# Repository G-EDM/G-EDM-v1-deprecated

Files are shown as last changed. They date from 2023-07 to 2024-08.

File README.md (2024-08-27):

Deprecated! Check the other repos for the new G-EDM EVOII stuff.

Check out the new Gantry router: https://github.com/G-EDM/GEDM-EVO2-CNC

# New design, new code, new sensing... Coming soon. 

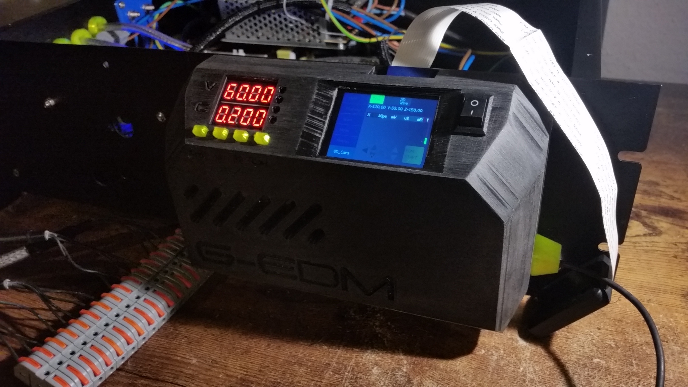
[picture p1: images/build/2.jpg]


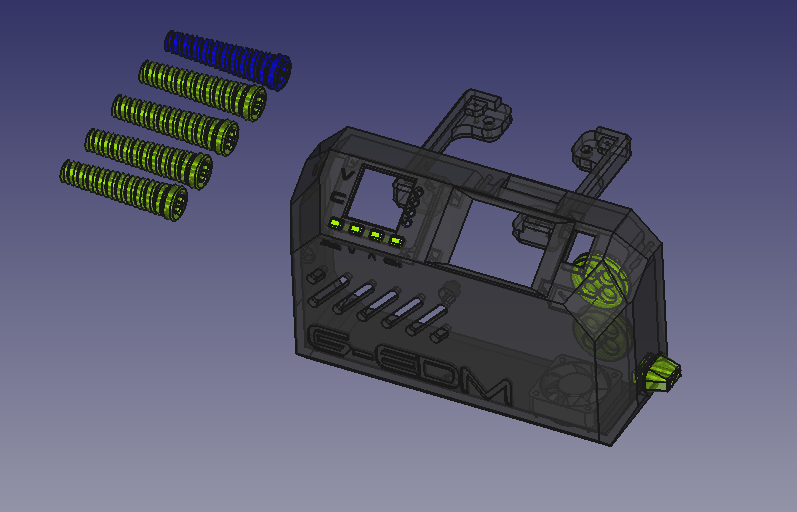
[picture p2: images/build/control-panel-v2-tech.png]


# Changelog

Added some parts to build a cheaper version:
    [>>> Entry level G-EDM <<<](https://github.com/G-EDM/G-EDM/tree/main/3D-files/G-EDM-Tower/printed-parts/work-in-progress/entry-level-gedm)

Added all 3D models to build the XY conversion 

Contact: goblin-dev@proton.me

# Let there be sparks... ⚡⚡⚡

```diff
  ██████        ███████ ██████  ███    ███  
 ██             ██      ██   ██ ████  ████  
 ██   ███ █████ █████   ██   ██ ██ ████ ██ 
 ██    ██       ██      ██   ██ ██  ██  ██ 
  ██████        ███████ ██████  ██      ██ 
```

# New: The wire EDM extension is working

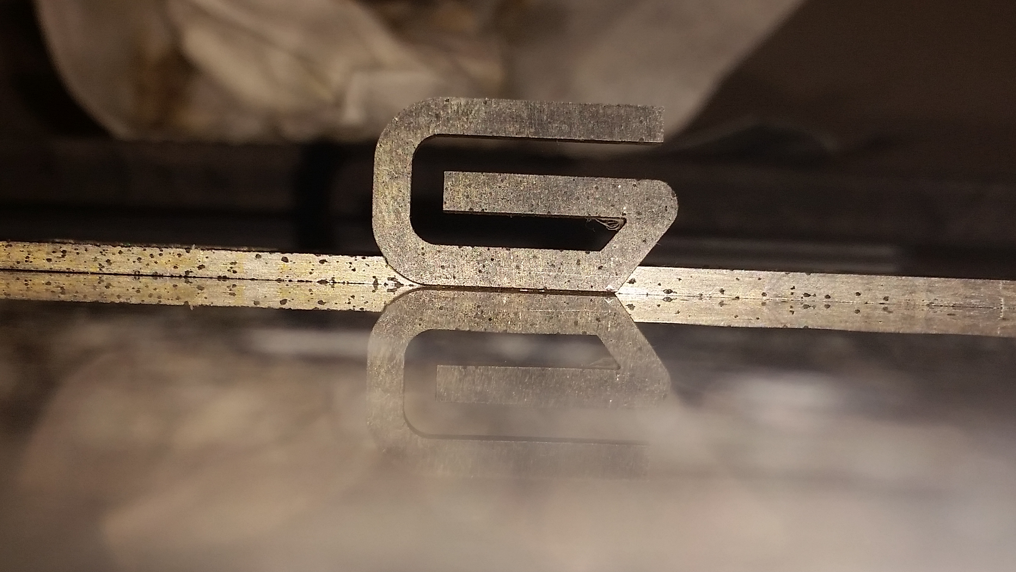
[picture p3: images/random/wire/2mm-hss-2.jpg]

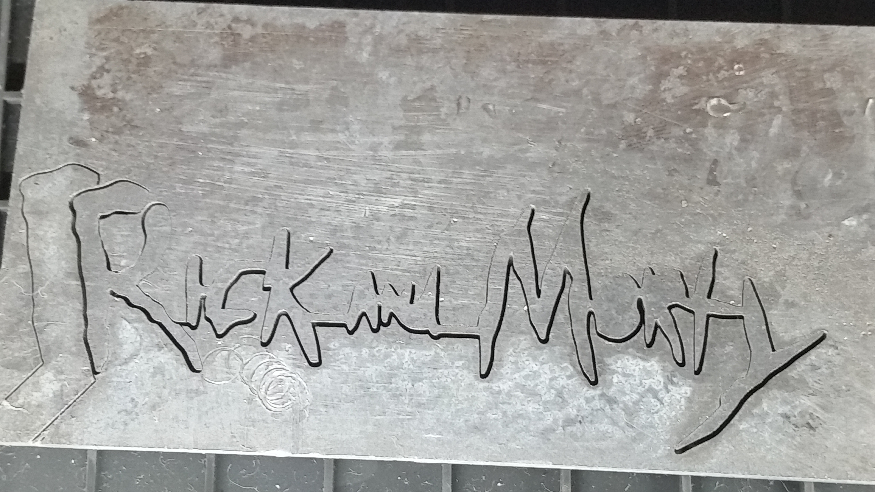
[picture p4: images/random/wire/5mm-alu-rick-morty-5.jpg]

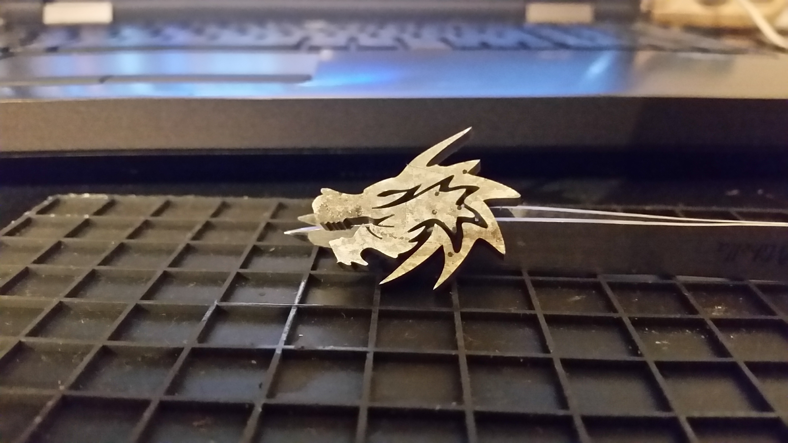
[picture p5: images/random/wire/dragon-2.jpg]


# About the G-EDM

    The G-EDM is a multi axis electrical discharge CNC machine that enables you to cut any kind of steel with just some electricity and water.
    EDM uses tiny electrical discharges to cut conductive materials and is a silent and precise way to create all kinds of shapes out of almost any kind of metal.

# Legal notes

    The author of this project is in no way responsible for whatever people do with it.

    No warranty. 

# License

    All files provided are for personal and private use only if not declared otherwise and any form of commercial use or redistribution of the protected files is prohibited. 

# Follow the project on youtube:

[>>> Follow the project on Youtube <<<](https://www.youtube.com/@G-EDM/videos)

[>>> Stay informed on Hackaday <<<](https://hackaday.io/project/190371-g-edm)

[>>> Join the Discord <<<](https://discord.gg/9cTsyDkEbe)

# Donations

    * Developement is not always as fast as it could be if you're poor. You want to donate something? 
    * Paypal: paypal.me/gedmdev
    * Bitcoin: bc1q9akp00a5hceh9n3jc9wfttxuwuk9c7da0sqkr8
    * Donations will be used for yoga stress relief sessions with joss sticks, thai massages, medication, therapy and burnout treatment
    * Some of your donations will be directed to the GRBL core developer team to support their great work. They may be happy about some yoga sessions too.
    
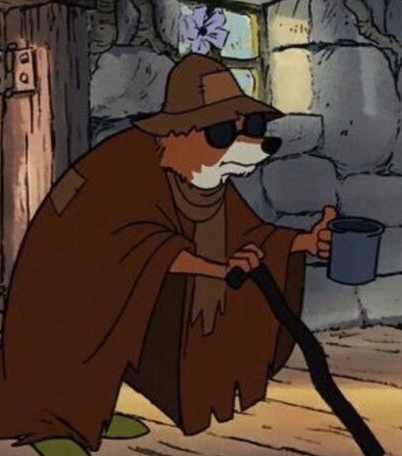
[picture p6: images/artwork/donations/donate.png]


# WARNING

An activated carbon airfilter is highly recommended. The spark of EDM can evaporate metals and may create some amount of metal fumes. 
It is also recommended to use gloves to handle the dirty water. If a waterfilter is used it may be a good advice to not open it after it fully dried out due to the super tiny metal particles created by EDM.

G-EDMs health tip: Don't smoke or drink metal. 

# The G-EDM

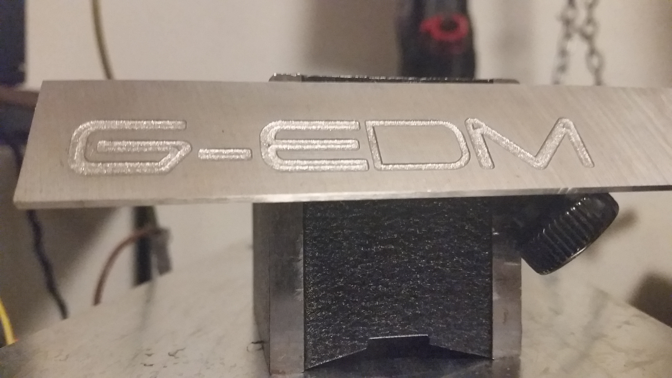
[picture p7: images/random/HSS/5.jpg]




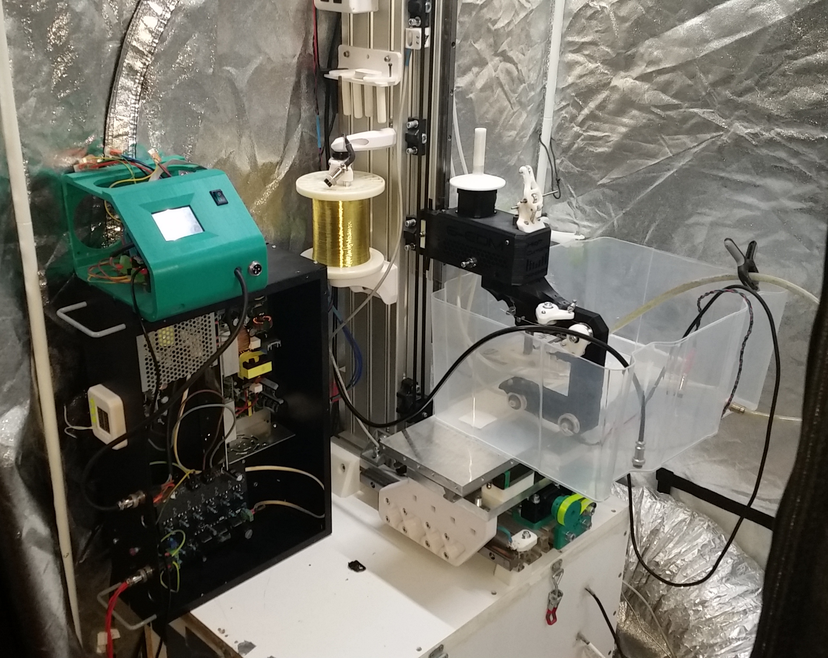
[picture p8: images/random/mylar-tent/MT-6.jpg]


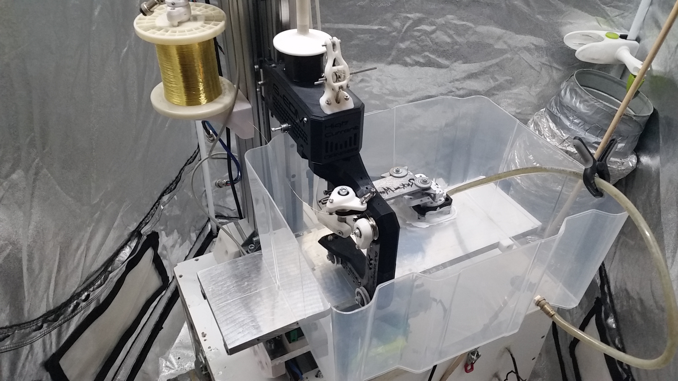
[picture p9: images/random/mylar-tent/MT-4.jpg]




This picture is not up-to-date. A lot has changed. The variable 30v bench PSU is not needed anymore and has been replaced by a 12v PSU that is mounted within the spark generator. This build can be used as single axis sinker/drill EDM but also as multiaxis CNC. Both is possible.

The old controlpanel has been replaced by a nice looking one with better cable management.



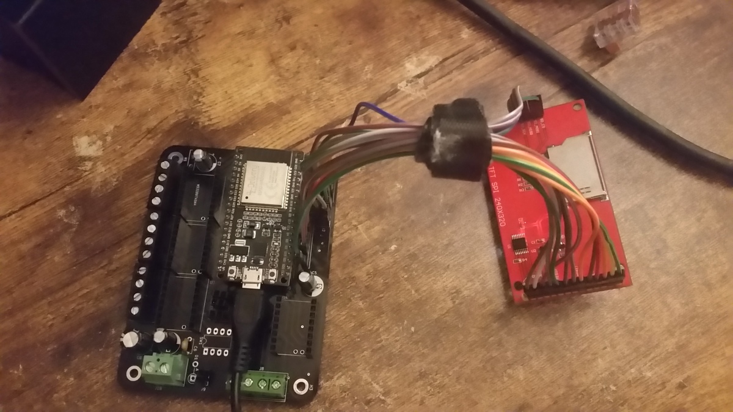
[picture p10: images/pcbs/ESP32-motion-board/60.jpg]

    
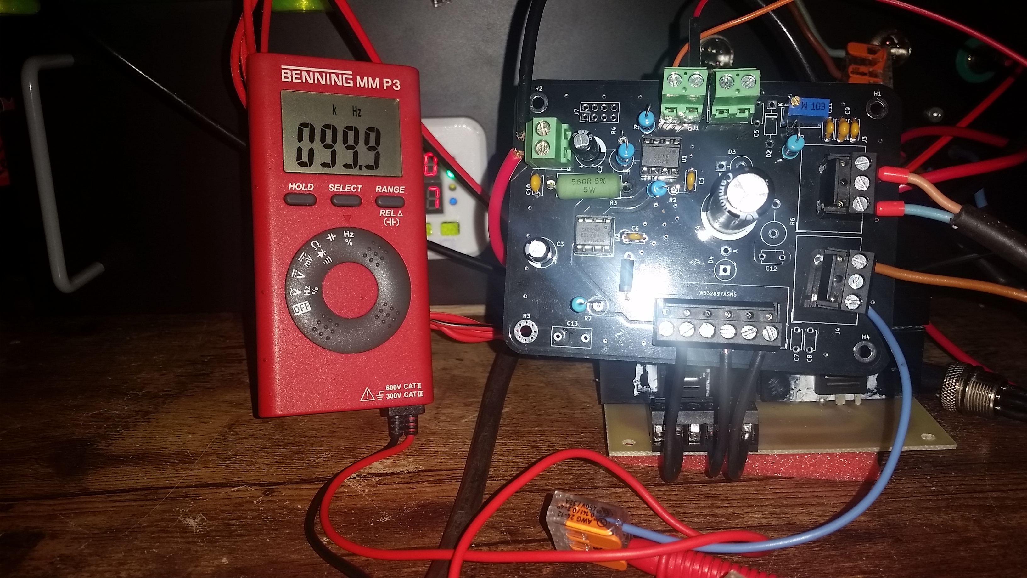
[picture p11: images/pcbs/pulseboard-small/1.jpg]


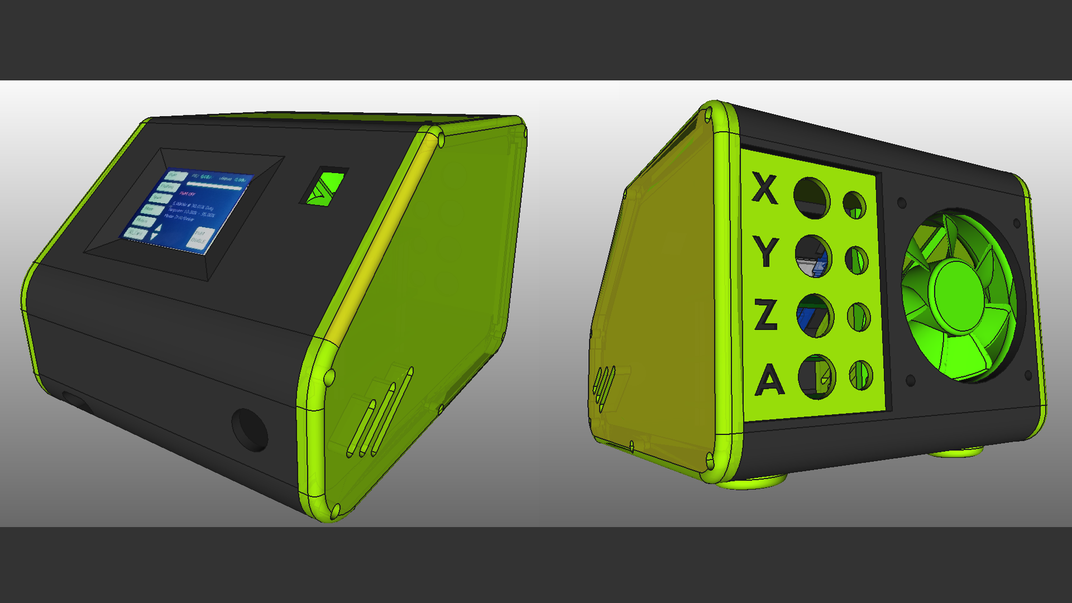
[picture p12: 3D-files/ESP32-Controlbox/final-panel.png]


# Other projects not related to the G-EDM

For those interested in a raw, low cost and cool looking desktop edm machine I can highly recommend to take a look at the picoEDM from @alextreseder

https://github.com/alextreseder/picoEDM



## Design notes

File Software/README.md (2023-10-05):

# Let there be sparks... ⚡⚡⚡

```diff
  ██████        ███████ ██████  ███    ███  
 ██             ██      ██   ██ ████  ████  
 ██   ███ █████ █████   ██   ██ ██ ████ ██ 
 ██    ██       ██      ██   ██ ██  ██  ██ 
  ██████        ███████ ██████  ██      ██ 
```

# Software section ( coming soon )

    * G-EDM GRBL Poem
    * Freecad post processor to create GCode for the G-EDM with Freecads Path workbench

# G-RBL

The gedm folder is copyright protected and not allowed to be used in any commercial ways and redistribution without permission is prohibited.

The grbl_esp32 folder is a highly modified version of grbl_esp32 and complies with the licensing they set.

The GEDM code is not a commercial product and is not sold, nor is it a ready to use product or compiled binary. It is not shipped with another product in any way. The code is not used in any GEDM products that may become available. It is just a beautiful poem on github that everyone can read and have fun with:

https://github.com/bdring/Grbl_Esp32/issues/1528#issuecomment-1749408457

All those points make it possible that the license of grbl doesn't affect the GEDM folder. 

The code is for private use and research only and not meant to be compiled. If it compiles at all.

# Stay informed:

[>>> Follow the project on Youtube <<<](https://www.youtube.com/@G-EDM/videos)

[>>> Follow the project on Hackaday <<<](https://hackaday.io/project/190371-g-edm)

[>>> Join the discord <<<](https://discord.gg/9cTsyDkEbe)

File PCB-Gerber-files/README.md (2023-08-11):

# Let there be sparks... ⚡⚡⚡

```diff
  ██████        ███████ ██████  ███    ███  
 ██             ██      ██   ██ ████  ████  
 ██   ███ █████ █████   ██   ██ ██ ████ ██ 
 ██    ██       ██      ██   ██ ██  ██  ██ 
  ██████        ███████ ██████  ██      ██ 
```

# Gerber files ( coming soon )

    * Gerber filepack for the ESP32 Motioncontroller
    * Gerber filepack for the small pulseboard with external Mosfet
    * Gerber filepack for the big pulseboard with 6 integrated Mosfets

    The gerber files provided are readily packed for PCBway.com

# Legal notes

    The author of this project is in no way responsible for whatever people do with it.

    No warranty. 

# License

    All files provided are for personal use only. Any form of commercial use is prohibited. 

# Follow the project on youtube:

[>>> Follow the project on Youtube <<<](https://www.youtube.com/@G-EDM/videos)

[>>> Follow the project on Hackaday <<<](https://hackaday.io/project/190371-g-edm)

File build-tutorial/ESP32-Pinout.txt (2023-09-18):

#######################################################
#
# GEDM ESP Pinout
# ESP32 WROOM 32 with 38 Pins with CP2102 
# https://www.amazon.de/AZDelivery-NodeMCU-Development-Nachfolgermodell-ESP8266/dp/B074RGW2VQ
#
#######################################################

   ### ILI9341 2.4" SPI TFT with Touch and SD card ###
   
   GPIO2  ---------------> CS
   GPIO4  ---------------> RESET 
   GPIO5  ---------------> SD_CS   
   GPIO15 ---------------> DC   
   GPIO18 ---------------> T_CLK,
                           SCK,       
                           SD_SCK
   GPIO19 ---------------> T_DO,
                           SDO<MISO>,
                           SD_MISO
   GPIO21 ---------------> T_CS
   GPIO23 ---------------> T_DIN,
                           SDI<MOSI>
                           SD_MOSI   
   3.3v   ---------------> LED, 
                           VCC
   GND    ---------------> GND
   
   ### TMC2209 Stepper drivers ###
   
   GPIO1   ---------------> DIR  ( Spindle stepper / A )   
   GPIO12  ---------------> STEP ( Spindle stepper / A )
   GPIO27  ---------------> STEP ( X )
   GPIO26  ---------------> DIR  ( X )   
   GPIO13  ---------------> STEP ( Y )
   GPIO14  ---------------> DIR  ( Y )   
   GPIO25  ---------------> STEP ( Z )
   GPIO33  ---------------> DIR  ( Z )   
   GPIO17  ---------------> MS1  ( Z )
   GPIO16  ---------------> MS2  ( Z ) 
   GPIO32  ---------------> ENA  ( Stepper enable pin shared by all steppers )   
   
   ### Others ### 
   
   GPIO39  ---------------> XYZ Limit switch  ( NC/Normally closed; wired in parallel. One wire to 3.3v and the other to GPIO39 )   
   GPIO22  ---------------> PWM  ( PWM for the pulsegenerator ) 
   GPIO34  ---------------> vSense Feedback In    
   GPIO36  ---------------> ON/OFF Switch ( NC/Normally closed; One wire to 3.3v and the other to GPIO36 )

   ### Notes ###
   
   TFT Display, Touch and SD Card are three different SPI devices that share one SPI bus. MOSI and MISO are data in and data out routes while
   the device is selected via the chipselect. So each SPI device has an own CS Pin but they all share MOSI, MISO and CLK. 
   GPIO18, GPIO19 and GPIO23 have three wires connected to each of them. 
   The motion PCB takes care of it and provides a PIN for each jumper wire. 
   If the machine is build without the G-EDM motion PCB it is possible to solder some jumper wires together to create a 
   3x female to 1x female adapter.

   GPIO36, GPIO39 (on/off and limit switch pins) are input only pins without internal pulldown features. 
                  They need an external 100k pulldown resistor. One leg to the pin and one to GND.
                  They also need a small ceramic capacitor to smoothen out the noise. 0.1uf

   The spindle stepper uses GPIO1 as DIR Pin. This was due to the lack of other output GPIOs.
   This means that any UART needs to be fully disabled. Serial/Uart communication changes the state of this pin.
   Since it is just a spindle it is possible to clip off the DIR pin on the TMC driver too.
   
   In the future this may change. For example MS1 and MS2 for Z is not really used anymore. Those two Pins would allow some more flexibility.
   Using fixed microsteps may be the best way.
   
   Also I haven't tested the GPIO1 as DIR pin yet since debugging the code needs massive communication and 
   I just don't have the time to remove all the debug stuff. I clipped off the DIR leg. :D

   The Pulsboard PWM GND/OUT is connected to the ESP GND Pin too. It is a shared GND between Pulseboard and Motionboard. 
   
   There are in total three  wires connected between ESP and Pulsboard: 
   
       ESP PWM Out to Pulseboard PWM In
       ESP vSenseIn to Pulseboard vSense Out
       ESP GND to pulseboard GND.

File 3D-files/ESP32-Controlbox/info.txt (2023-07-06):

The big enclosure body was printed with PLA+ flipped 90° to the left with the biggest brim possible and some large antiwarping patches. Hairspray on the bed helps alot.

Printed with zero supports. The displaywindow was just bridged. No problems.

The top lid can be printed with the text down and again without supports.

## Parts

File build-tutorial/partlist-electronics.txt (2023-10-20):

# Requirements

Don't bother with 30-60W soldering irons. The board uses power and gnd planes without thermal reliefs. The connections between the legs and the planes are fully filled and the heat applied will spread rapidly across the planes. A 30W soldering iron will not be able to keep up with this. It can be done somehow but I don't recommend it.

I use this soldering iron with the a big (not small not medium but BIG ) 4mm single flat tip. The small tips again won't do it for connections to the gnd and power plane, but will work for the non plane connections. Only use higher power if needed! If a contact seems hard to solder the power can be increased. For all other contacts normal power is ok.

This one has 90W and it is still a little to weak to solder the big terminals on the big planes. 120W would be better. I just used two irons (90W+60W) to get a nice connection. 

https://www.amazon.de/Elektrische-gesteuertem-automatischem-Schlafmodus-elektronische/dp/B09KGCSG83
 
And a set of tips with the big tip needed (900M-T-4C 4mm bevel):

https://www.amazon.de/RMENOOR-L%C3%B6tkolbenspitzen-L%C3%B6tspitzen-Schwei%C3%9Fh%C3%BClse-L%C3%B6tstation/dp/B07VSDP5MH

# Tools and useful parts

* Tools

    - 1x A cheap Multimeter
    https://www.amazon.com/Neiko-40508-Digital-Multimeter/dp/B00066ZZO4
	- 1x 60W soldering Iron
	https://www.amazon.com/Soldering-Ceramic-Adjustable-Temperature-Repairing/dp/B09DSDBC7G
	- 1x solder wire
	- 1x set shrinking tube
	- 1x set wire end ferrules with crimp tool
	https://www.amazon.com/WEKESIGO-Crimping-Self-adjustable-Terminals-Connectors/dp/B0B39BLVSH

# Parts needed for spark generator

* Case

    - Metal case; I use a 19" 3U ( 440 x 290 x 132 mm ) rack mount server case
    It needs to be metal to shield the EMI noise and offer enough room to add one or two fans for good ventilation.

* Power supplies

    - 1x 65V 12.3A 800W LED Switch Power Supply
    https://www.amazon.com/NVVV-Transformer-Security-Printer-Computer/dp/B09L4JBKPV

    - DPM-8605 60V 5A step down module ( to control voltage and amps of the PSU )
    https://www.amazon.com/DPM-8605-485-Programmable-Communication-Step-Down-Converter/dp/B0BC8PHF2Z

    - 12V 10A PSU ( to provide the power for the steppers and the pulseboard )
    https://www.amazon.com/LEDMO-Switching-Converter-Adapter-Transformer/dp/B01E6RMASC

    - A power plug with 3 Wires ( Hot/Neutral/Ground )
    Choose the biggest wire possible. 14 AWG should be fine for this build. If possible 12 AWG.
    It will deliver power to both PSUs. The 12v and the 65v. The DPM limits the 65V PSU to 5Amps. The steppers run at about 1.5A each depending on the microsteps. 

    - 2 banana jacks ( one red one black )
    Not all of them are isolated. If they're not isolated they cannot be mounted directly onto the metal case and need a printed mounting plate as isolation from the box.
    https://www.amazon.com/Banana-Female-Binding-Adapter-Connectors/dp/B07C7WG23G

    - Aligator clips with banana plugs on one side; 15A
    https://www.amazon.com/Banana-Crocodile-Alligator-Probe-1000V/dp/B083DN3RQL

* Misc

    - 4x bass hex standoffs ( to mount the raw DPM8605 PCB; can be 5-20mm )
    - 4x brass hex standoffs ( Lenght depends on the size of the heatsink )
    https://www.amazon.com/XLX-Male-Female-Female-Female-Assortment-Stainless/dp/B07ZSYDGR6

# Parts needed for the control panel

* Display

    - 1x ILI9341 SPI Touch 2.4" 240x320 ( There are many different version. Some are larger in size even if the display is 2.4" and some don't have touch and some others use an 8Bit parallel bus instead of SPI. The GEDM needs the SPI version!)
    https://www.amazon.com/HiLetgo-Display-ILI9341-Touch-240x320/dp/B07WNLNRDN
    
    ### WARNING ###
    This one does not work. It uses an 8Bit parallel bus and we need SPI:
       HiLetgo 2.4" ILI9341 240X320 TFT LCD Display with Touch Panel LCD for Arduino UNO MEGA2560 

* Wires

    - A set jumper wires 20cm female-to-female ( To connect the display to the PCB )
    - A set jumper wires 20cm male-to-female ( To connect the switches, vSense, PWM )
    - AWG21 or 0.75mm wire ( to connect the stepper motors to the terminals )
    - AWG16 or 1.5mm ( to connect the 12v motor power from the spark generator to the control panel )

 + Connectors

    - 7x 4-Pin GX16 aviation sockets and plugs

    Best to buy a pack of 10 or two packs of 5:
    https://www.amazon.com/Yowming-Aviation-Thread-Female-Connector/dp/B07HT76HG6

    - 1x Set DC connectors and sockets ( used for the limit switches )
    https://www.amazon.com/Socket-Threaded-Connector-Adapter-Dustproof/dp/B08SJM2G52

    - Some 2 port WAGO connectors
    https://www.amazon.com/WAGO-221-412-Lever-Nuts-2-Conductor-Connectors/dp/B07W4RQ6R6

    - Some 5 port WAGO connectors 
    https://www.amazon.com/WAGO-221-415-Lever-Nuts-5-Conductor-Connectors/dp/B07W7W9J96

* Switch

    - !x On/Off rocker switch ( Used to start/stop the EDM process )
    https://www.amazon.com/TWTADE-Solder-Rocker-Switch-KCD1-X-F/dp/B07XD8J2PL

* Misc

    - 4x 10mm brass hex standoffs
    https://www.amazon.com/XLX-Male-Female-Female-Female-Assortment-Stainless/dp/B07ZSYDGR6

##########################################################################################
##
## Note: There are two version of the pulseboard available. They both work different
## The small one has the mosfets separated and uses a DIP8 gate driver to switch them
## The big version uses a discrete push/pull gate driver circuit based on bjt power transistors
## and supports up to 6 mosfets integrated on the PCB. It also has some indicator LEDs.
## The total costs of the parts are nearly the same except for the PCBs itself. The big PCB is roughly double the price due to double the size
## I think the big one is easier to build and the LEDs just look cool.
##
##########################################################################################

###############################################################
##
## Parts needed for the small pulseboard with external mosfets
##
###############################################################

* Gate driver

    - 1x MCP14E9-E/P 3,0A Dual-MOSFET-Driver, 2 x iverted, DIP-8

* Resistors

    - 1x 1k 1W ( used as current limiting resistor for the vSense feedback )
    - 1x 4.7K 1W
    - 1x 10k 
    - 1x 560R 5W 
    - 1x R470 1W
    - 1x R220 1W ( current limiting resistor to protect the ESP PWM Pin )

* Capacitors ( If it needs to be low ESR it will be listed as such. If it is not listed as low ESR then don't use low esr. )

    - 1x 100uF >100V photo flash capacitor ( a normal low ESR capcitor should work too )
    - 2x 47uf 63v capacitors ( voltage rating can be lower too and is not critical )
    - 3x 100pF (or larger) 500V ceramic disc capacitors 5mm grid; ( CT81 high voltage ceramic capacitor is what I use. It needs to be >100v and < 0.1uF )
    - 3x 100nf 50V ceramic disc capacitors 5mm grid;
    https://www.amazon.com/BOJACK-Capacitor-Multilayer-Monolithic-Assortment/dp/B085RLXXBK

* Diodes

    - 1x 1N5352B 15V 5W Zehner diode for gate protection ( 15v is good but 18v may be a better choice )

* Optocoupler

    - 1x 6N136 Optocoupler ( Note: This board doesn't use the 6N137 optocoupler like the big pulseboard does )

* Terminals

    - 3x 2 pole screw terminals; 5mm grid ( 12v supply power, PWM in and vSense in/out )
    https://www.amazon.com/DAOKI-Sockets-2-54MM-Adapter-Solder/dp/B07YKGJ6QG
    
    - 2x 2 pole terminal; 10mm grid ( spark in/out and spark power in/out; 3 pole 5mm grid terminals work too if the center pin is clipped off )
    https://www.amazon.com/uxcell-Pluggable-2-Position-Mounting-Connector/dp/B00NWE2N9M

    - 1x 3 pole terminal; 10mm grid ( to connect the mosfet; a 5 pole 5mm grid terminal will work too if every second pin is clipped off )
    https://www.amazon.com/Heyiarbeit-Terminal-Tinning-Connector-MG55C-10-0/dp/B08ZXBPW5S/

* Dip sockets

    - 2x DIP8 socket ( to easily plug in the optocoupler and the gate driver )

* Poti

    - 1x 10k Ohm 3296 Trim Pot 
    https://www.amazon.com/uxcell-Through-Hole-Trimmer-Potentiometer/dp/B008LT4IGY

###############################################################
##
## Parts needed for the big pulseboard with integrated mosfets
##
###############################################################

+ BJT Transistors

    - 1x PNP 2SB688 BJT power transistor
    - 2x NPN 2SD718 BJT power transistor
    This set will do:
    https://www.amazon.com/2SB688-Bipolar-Junction-Transistor-Assortment/dp/B08LVGMNB4

* Mosfets

    - 6x IRFP260N or similar Mosfet in TO-247AC package ( the board can take 6 of them. But it is not needed to use all six. )
    https://www.amazon.com/Bridgold-IRFP260NPBF-IRFP260N-IRFP260-Transistor/dp/B07R49H4HZ
    - 6x TO-247 insulation sheets and shoulder washers to prevent the screw from touching the mosfet cases drain
    https://www.amazon.com/Electronics-Salon-Silicon-Insulator-Bushing-Assortment/dp/B017AS9DM0

* Heatsink

    - 1x Heatsink that covers all 6 mosfets. 140mm lenght would be perfect but couldn't find any. 130mm could work too but it would make the outer mosfets sitting on the total edges of the heatsink. Don't like it.
    https://www.amazon.com/LuoQiuFa-Aluminium-Heatsink-Radiator-Computer/dp/B0B1CDPJDT 

    ( I haven't mounted any heatsink at the moment. Need to get one first too. For short testing with 1A this is ok but only for short testings. The mosfets get hot very fast and and at some point: Problem. )

* Optocoupler

    - 1x 6N137 Optocoupler

* Dip sockets

    - 1x DIP8 socket ( to easily plug in the optocoupler )
    https://www.amazon.com/DAOKI-Sockets-2-54MM-Adapter-Solder/dp/B07YKGJ6QG

* LEDs

    - 1x 3mm LED blue 3.2v ( Used as power indicator )
    https://www.amazon.com/GFORTUN-Emitting-Diffused-Electronic-Indicator/dp/B08D3T25H5

    - 1x 3mm LED green ( low current LED! Used as PWM indicator. Optional. )
    https://www.amazon.com/Kingbright-Led-Green-2Mcd-568Nm/dp/B08X1HXHXG

* Diodes

    - 6x SB 140 DIO Schottkydiode, 40 V, 1 A, DO-15 ( fast turn-off diodes for the mosfet gates )

* Resistors

    - 1x R560 5W axial ( length: 17mm; dia: 6mm )
    - 1x R560 2W
    - 6x R4.7 2W ( Used as gate resistor. This value could change to 6.8Ohm 2W later. Maybe it works better. )
    - 6x 100kOhm 1W ( Used as pulldown for the Mosfet gates )
    - 1x R220 1W ( used as current limiter for the PWM signal to the optocoupler )
    - 1x R200 1W ( used as current limiter to the PWM indicator LED. Can be R220 too. )
    - 2x 4.7kOhm 2W
    - 1x 1kOhm 1W
    - 1x R560 1W (used as current limiter for the 12v power indicator LED )

    Not all 1W sets have a R200 resistor. This one has:

    https://www.amazon.com/AUKENIEN-Assortment-Resistors-Compliant-Electrical/dp/B09SZBQWV4

* Capacitors ( If it needs to be low ESR it will be listed as such. If it is not listed as low ESR then don't use low esr. )

    - 3x 100pF (or larger) 500V ceramic disc capacitors 5mm grid; ( CT81 high voltage ceramic capacitor is what I use. It needs to be >100v and < 0.1uF )
    - 3x 100nf 50V ceramic disc capacitors 5mm grid;
    https://www.amazon.com/BOJACK-Capacitor-Multilayer-Monolithic-Assortment/dp/B085RLXXBK

    - 1x 100uF >100V photo flash capacitor or LOW ESR
    - 2x 680uf 25v capacitor 8mm diameter; 5mm grid
    - 1x 220uf 100V capacitor; 7,5mm grid; (this one is used a bulk capacitor on the 12v terminal. Using different ones should be ok but this is the one used on the protoype and therefore it will be kept as recommend until other caps are confirmed working)

* Terminals

    - 3x 2 pole screw terminals; 5mm grid ( 12v supply power, PWM in/out and vSense out )
    - 2x 2 pole terminal; 10mm grid ( spark in/out and spark power in/out; 3 pole 5mm grid terminals work too if the center pin is clipped off )
    https://www.amazon.com/uxcell-Pluggable-2-Position-Mounting-Connector/dp/B00NWE2N9M

* Poti

    - 1x 10k Ohm 3296 Trim Pot 
    https://www.amazon.com/uxcell-Through-Hole-Trimmer-Potentiometer/dp/B008LT4IGY

###############################################################
##
## Parts needed for the ESP32 controller PCB
##
###############################################################

* External boards

    - 1x ESP32 38Pin WROOM-32 NodeMCU Dev Kit C Development Board with CP2102
    https://www.amazon.de/AZDelivery-NodeMCU-Development-Nachfolgermodell-ESP8266/dp/B074RGW2VQ
    - 4x TMC2209 v2.0 ( For the sinker only build 2 of them will do. 1 for Z and 1 for the spindle )
    Note: Those drivers are originally designed by watterott and called SilentStepStick
    They shared the design with the opensource community and now a lot of clones are sold on Amazon.
    If you want to support them for their great drivers buy the original boards:
    https://github.com/watterott/SilentStepStick
    https://shop.watterott.com/SilentStepStick-TMC2209-V2

    It is important to use the v2.0 version of those drivers. They have a better chip and a bigger heatsink (14,5 x 15 x 13). They are able to handle more current. And a small warning: They are supper sensitive and can be damaged easily. Never move the stepper by hand while the drivers are connected. The reverse voltage can damage the drivers.

+ Screw terminals

	- 1x 2 pole terminal 5mm grid ( for 12v power > 10A )
	- 4x 4 pole terminal 5mm grid ( to connect the steppers. One for each axis )

* Pin sockets

	- 2x 1x19 Pin Sockets ( to plug in the ESP32 )
	- 8x 1x8  Pin Sockets ( to plug in the TMC2209 drivers )

    These sets will work. They don't have the exact pin number needed but it is possible to cut them to size:
    https://www.amazon.com/Glarks-Straight-Connector-Assortment-Prototype/dp/B076GZXW3Z

* Pin headers

	- 1x 1x11 Pin Header
	- 9x 1x2  Pin Header
	- 1x 2x2  Pin Header ( this one is a two row header 2x2 pins. It is possible to use 2 1x2 headers too )

    These will work for the single row pin headers and can be cut to size:
    https://www.amazon.com/HiLetgo-20pcs-2-54mm-Single-Header/dp/B07R5QDL8D
    
* Jumper caps

        - 2x 1x2 jumper cap - low height

    Note: In the example images there where pin sockets used instead of pin headers. It works too but is not recommended. The jumper wire pins won't hold very tight in these sockets.

* Capacitors ( If it needs to be low ESR it will be listed as such. If it is not listed as low ESR then don't use low esr. )

	- 1x 680uf 25v capacitor 8mm diameter; 5mm grid );
	- 1x 680uf 16 or 25v capacitor max 8mm diameter; 5mm grid;
	- 1x 47uf 50v capacitor; 5mm grid;
	- 3x 100nF 50v ceramic disc capacitor; (104)

* Resistors

	- 2x 1k   1/2W resistor
	- 3x 100k 1/2W resistor ( Buy 3 of them. Maybe one is used later for the vSense input pin )
	( The build images show larger resistors but they are heavily oversized )

* Dip switch

	- 1x 4 pole dip switch ( to set the microsteps for XY and A )

	https://www.amazon.com/Comidox-Position-Switch-Module-Terminals/dp/B07LBMC9HV

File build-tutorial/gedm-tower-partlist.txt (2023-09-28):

#####################################################
#
#
# This list may not be complete and with all the changes done so far
# it is possible that some of the small parts are not needed anymore
#
#
#####################################################

#####################################################
####
#### Parts for the shielded spark generator
####
#####################################################

Shielded enclosure:

  1x 19" 3U rack mount case 300mm deep ( plenty of room for everything )

  ( You can use a big scooby doo metal lunchbox to archive the needed RF/EMI shielding too. Whatever floats your boat )

Main PSU:

  1x 65V 12.3A 800W LED Switch Power Supply Driver AC 110/220V to DC 65V Transformer for LED Strip CCTV Security System,Camera,3D Printer,Computer Project,Motor

Motor PSU ( powers the steppers, the pump, the spindle motor and the mosfet gate driver ):
  
  1x AC 110V/220V to DC 12V 10A 120W Universal Regulated Switching Power Supply Adapter Transformer Driver Converter for LED Strip Light, CCTV Security Camera System, Computer Project 

Step down converter to control voltage and current:

  /** 
    *
    * If money is no issue I recommend the bigger one. 
    * I use the small one that can deliver a maximum of 5A which I'm happy with
    *
    **/

  Programmable DC Numerical Control Power Supply
  1x DPM8605; 0 - 60v; 0 - 5A; 300W

  or
  
  /** that is a lot of power and it is easy to burn the mosfets with this **/
  1x DPM8624 0 - 60 V 0 mA - 24 A 1400 W 

Ventilation:

  1x 12v 120mm Fan

Connectors:

  1x 4mm banana plug sockets; 1x red and 1x black;
  1x 4mm banana plugs; 1x red and 1x black;
  1x GX16 aviation socket; 4 pin;
  2x GX16 aviation plug; 4 pin;

Some WAGO terminals

Some M3, M4, M5, M6, M8 screws, nuts and T-slot nuts and a set of setscrews.

#####################################################
####
#### Other Parts
####
#####################################################

  1x 12v Peristaltic Pump 3mm x 5mm silicone tubing. 150ml/min 
  1x 3mm x 5mm silicone tube; 2 meters;
  The diameter of the silicone tube is important if it is used with the round bar drill jig. 150ml/min seems to work "ok".

1x Touch display 320x240 ILI9341 2.4" 

      There are different models available. It is important to choose the correct one. Some have larger PCBs.
      This display is available without tuch too. Touch is needed!
    
    HiLetgo 2.4" SPI TFT LCD Display 2.4 Inch ILI9341 Touch Panel LCD ILI9341 240x320 5V 3.3V

6x DC Power Sockets and plugs 

    5.5 x 2.1 mm DC Power Jack Socket Threaded Female Panel Mount Connector Adapter 
    with Dustproof Plug 6Pack 

1x On/Off rocker switch. 2poles. For 13mm*19mm pocket. ( A 5 Pack is good to have )

    On/Off Boat Rocker Switch 5Pcs 2 Pin Position Snap 12V 110V 250V QTEATAK 

3x Micro limit switch ( A pack of 25 is good to have. They are cheap )

    Cylewet 25Pcs AC 1A 125V 3Pin SPDT Limit Micro Switch Long Hinge Lever for Arduino (Pack of 25)

7x Aviation Connector Plugs and sockets GX16 4PINs ( They are available with 2,3,4,5 Pins. We need the 4 Pin version )

    Aviation Connector Plugs, Lsgoodcare 30Pcs 16MM 4 Pin Din Female/Male Aviation Wire Connector Plug, AC 200V 5A GX16-4 Pin Metal Chassis Thread Panel Connector Socket 

2x Banana sockets and plugs. One red and one black ones for 8mm hole.

    10Pcs Black and Red 4mm Banana Jack Socket Female Adapter Panel Mount Binding Post for 4mm Banana Plug Connectors 

2x 4mm Banana plugs. One red and one black. 

A big set jumper wires. 10cm and 20cm. Male to male and male to female for both sizes.

4x Standoff Male/Female 10mm 
4x Standoff Male/Female 20mm
4x Standoff Male/Female 30mm 
4x M3 Nut
4x M3x6 Screw

    Csdtylh 320Pcs M3 Motherboard Standoffs&Screws&Nuts Kit, Hex Male-Female Brass Spacer Standoffs, Laptop Screws for DIY Computer Build, Electronic Projects, Raspberry Pi, Circuit Board etc.

## To mount the limit switches ##

4x Screws M5x8
4x T-Nut M5 Slot6 
4x M2x12 Screws
4x M2 Nut

#####################################################
####
#### Mechanical Parts
####
#####################################################

PLA+ and a little TPU for a small belt.

C12-ER11M-100L ( hollow and needs to be cut to 80mm length )
I used this one that is hollow by default: https://www.amazon.de/dp/B087N5H9T4?psc=1&ref=ppx_yo2ov_dt_b_product_details
The shaft slides into the bearings and needs one or two shaft collars with 12mm inner diameter.

2x 6201Z 12x32x10mm bearing ( one is pressed into the top lid and one into the main tool head )
4x 684ZZ Ball bearings for the printed idler pulley
2m GT2 Timing belt. 6mm width. Use a set that comes with the aluminum clamp mount block/bar that is needed.

Aluminum extrusions:

Base plate:
160x40 Slot 8; 400mm length; Heavy or Eco variant; M8 Thread on one side in the two center holes;

Z axis:
1x 120x80 Slot 8mm; 750mm length; Heavy or Eco variant;
1x 20x40 Slot 6mm; 400mm - 600mm length; For more worktravel use 600mm;

Linear rails:

Z-Axis:
HGR15 with 1x HGH15CA sliding block, Same length as the small extrusion; 400mm -600mm; 

Mounting parts:

The big Z Beam rests on the base plate and is connected with two angle brackets and a aluminum plate at the back.

2x 40x40 90° brackets for Slot 8 profiles
1x 150x80x10 Aluminum plate

Some T-Nuts for Slot 8 and 6 slots:

20x Slot-8 M8
20x Slot-6 M6
Slot-6 M3 (number depends on the length of the linear rail)

A package of setscrews and a box of different hex screws. M2, M3, M4. Also some M6 and M8 Screws are needed.
T Slots Nuts for M6, M8, M4. I don't use the small ones. Only the heavy squaretype ones.

M8 and M6 screws. Don't know the exact size
M8
4x M8x18 
6x M8x25
6x M8x30
M6
12x M6x15

M3
M3x8 ( number of screws depends on the linear rail length you choose )

Stepper:

Z-Axis:

# Dual shaft stepper for the spindle and wire rewinder
Nema 17; 0.4Nm; 1.68A; 1.8° Step angle; 5mm shaft; Rated 2.8v; DUAL SHAFT is needed if the machine is used with the wire extension!
The stepper I use: SY42STH47-1684B
 
# Stepper for the axis 
Nema 17 planetary gearbox; 19.2:1; 8mm shaft; ( if you can't get the exact 19,2:1 gear ratio you can use 19:1 or similar; This can be adjusted in the software)
https://www.reichelt.de/schrittmotor-hoch-drehmoment-hybrid-2-phasen-nema17-01-p219027.html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

For the strong roundbar drill jig an aluminum tube is needed with 40mm OD and 32mm ID. Currently only supports 12mm round bars.

This list may not be complete. Some screws and maybe other parts needed could be missing here. 

# XY Axis

2x Nema 17; 0.4Nm; 1.68A; 1.8° Step angle; 5mm shaft; Rated 2.8v; I use: 17SY42STH47-1684A

    https://www.reichelt.de/schrittmotor-hoch-drehmoment-hybrid-2-phasen-nema17-01-p219027.html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

* Linear rails
    * 1x HGR20 500mm + 2x HGH20CA linear block + SFU1605 Ballscrew 450mm ( ~80.- )
    * 1x HGR20 300mm + 2x HGH20CA linear block + SFU1605 Ballscrew 250mm ( ~80.- )

* Aluminum
    * 1x 150mm x 530mm x 15mm ( ~70.- )
    * 1x 150mm x 260mm x 15mm ( ~40.- )

#####################################################
####
#### Wire EDM extension V2
####
#####################################################

Bearings:

2x MR63ZZ 3x6x2.5mm
7x V623ZZ 3x12x4mm bearings

4x 696-2RS Kugellager seald 6x15x5mm 
https://www.amazon.de/dp/B09V5DBM6Y?psc=1&ref=ppx_yo2ov_dt_b_product_details

4x v groove bearing 6x30x8mm (2.5mm groove depth. They are sold as 8mm width but the center is 9mm and only the outer ring is 8mm. Integrated washers)
https://www.amazon.de/dp/B076VCCCMS?psc=1&ref=ppx_yo2ov_dt_b_product_details

2x Pneumatic fittings with M10 thread
https://www.amazon.de/dp/B07DGLCJ4Z?psc=1&ref=ppx_yo2ov_dt_b_product_details

1x set with 3D printer nozzles

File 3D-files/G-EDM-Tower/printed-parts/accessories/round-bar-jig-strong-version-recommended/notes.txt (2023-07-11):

This jig can be used to drill 12mm round bars like axles or the shafts of C12-ER16 collet chucks to use them with internal waterflow.

The reamer chuck can be used to enlarge the bore. In reamer mode the water flows from the bottom through the pilot hole while z moves up and down.

For deep holes the normal brass tubes won't work very good if the inner diameter is too small. There are special EDM tubes available that have multiple tubes pressed into a normal tube. This prevents a long tiny metal spike that builds up with normal tubes and cloggs it at some point.

The deeper the hole is the better the pump should be. Low flow is ok if it has enough pressure. For my purposes the 12v peristaltic pump works. A second one in series would produce more pressure.

Aluminumtubes are not precision parts. My 40mm OD x 32mm ID tubes are 40mm x 32.1mm. So I needed oversized parts. The parts are named. Choose the size that fits your need.

Add some gluestick or strong hairspray to the printbed for the big pipe stand and a 20mm brim. Without it will wrap heavily 100%.

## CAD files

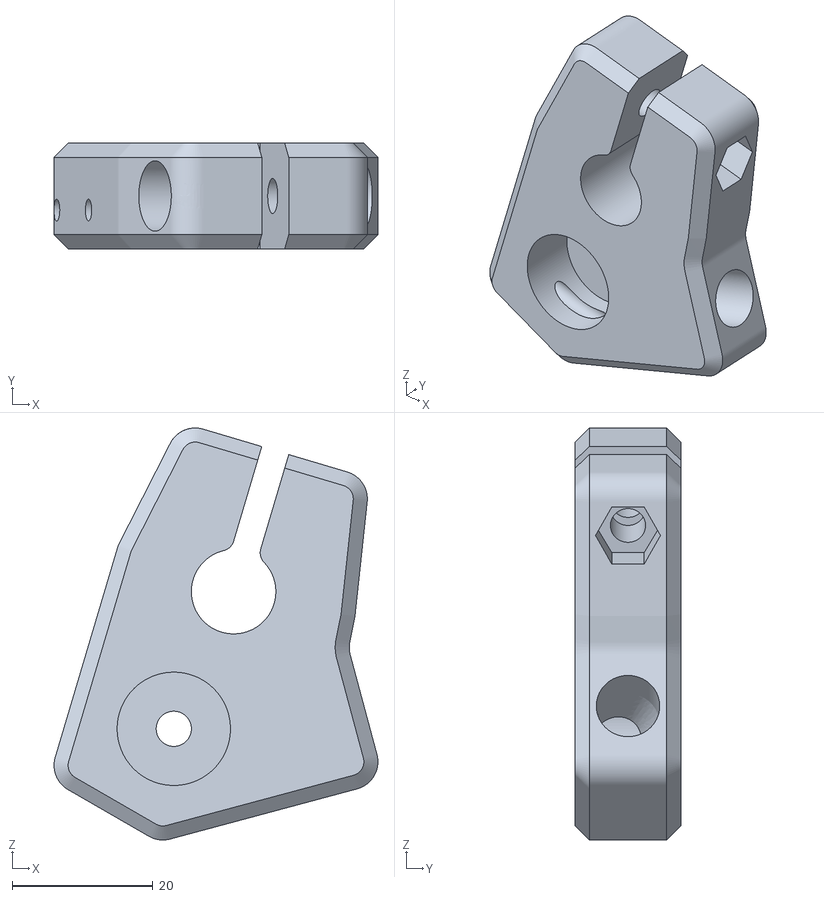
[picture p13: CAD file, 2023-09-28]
3D-files/G-EDM-Tower/printed-parts/work-in-progress/wire-extension/wire-extension-v2/adjustable-wire-guide-main.stl
46.0 x 15.0 x 58.6

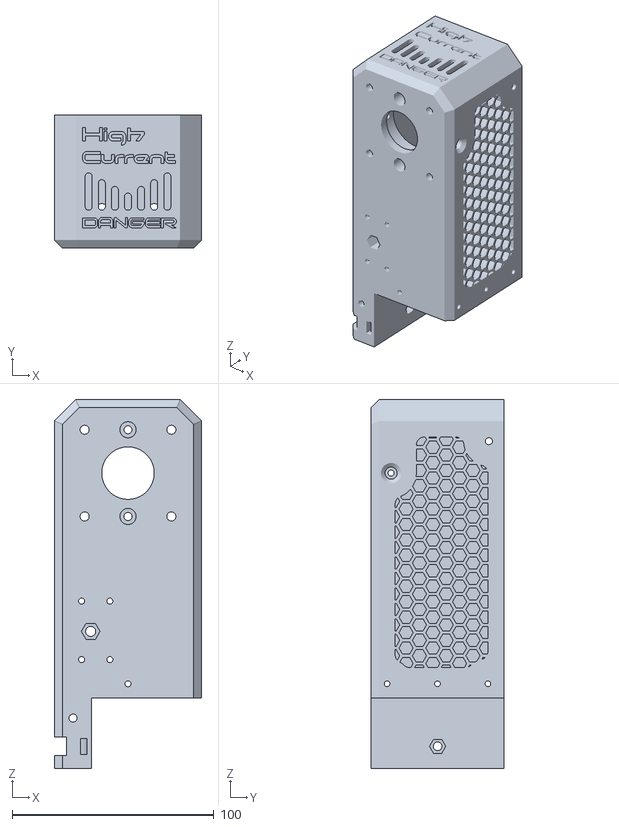
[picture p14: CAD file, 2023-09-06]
3D-files/G-EDM-Tower/printed-parts/z-axis/HGR15-Toolhead/z-axis-tool-head-main-HGR15-v3.stl
73.0 x 66.0 x 183.0

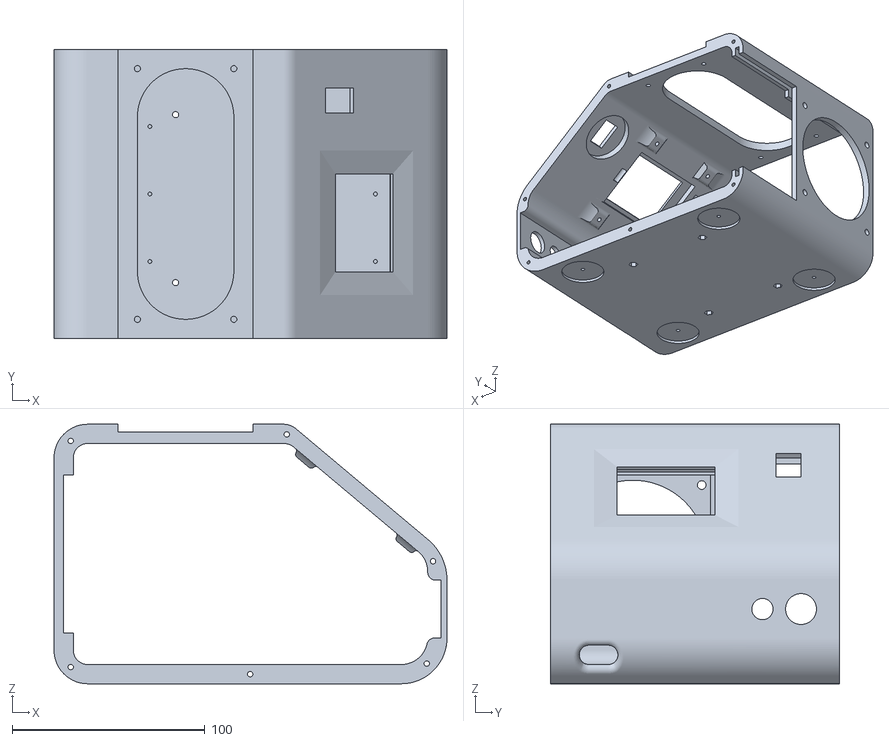
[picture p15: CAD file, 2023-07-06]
3D-files/ESP32-Controlbox/Control-panel-main-body.stl
203.8 x 150.0 x 134.6

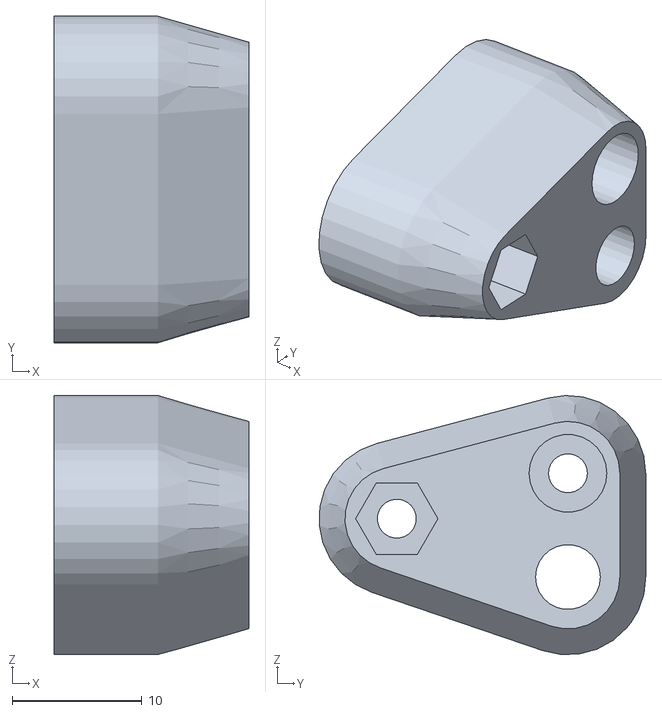
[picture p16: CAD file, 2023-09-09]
3D-files/G-EDM-Tower/printed-parts/work-in-progress/wire-extension/wire-extension-main-brake-system.stl
15.0 x 25.2 x 20.0

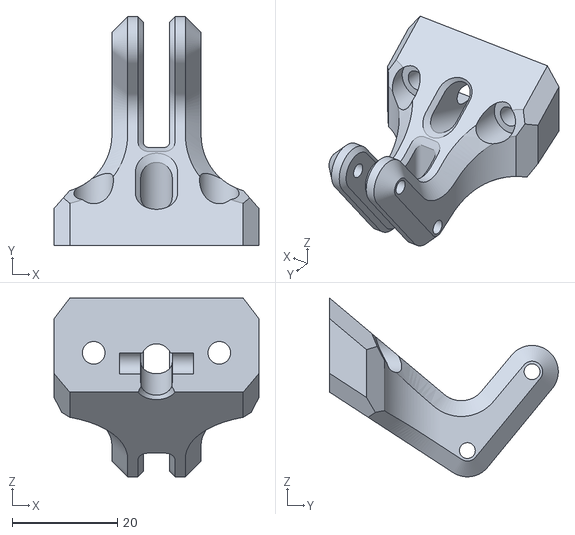
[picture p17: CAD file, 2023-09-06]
3D-files/G-EDM-Tower/printed-parts/work-in-progress/wire-extension/rewinder-wire-guide-main.stl
39.0 x 43.5 x 34.0

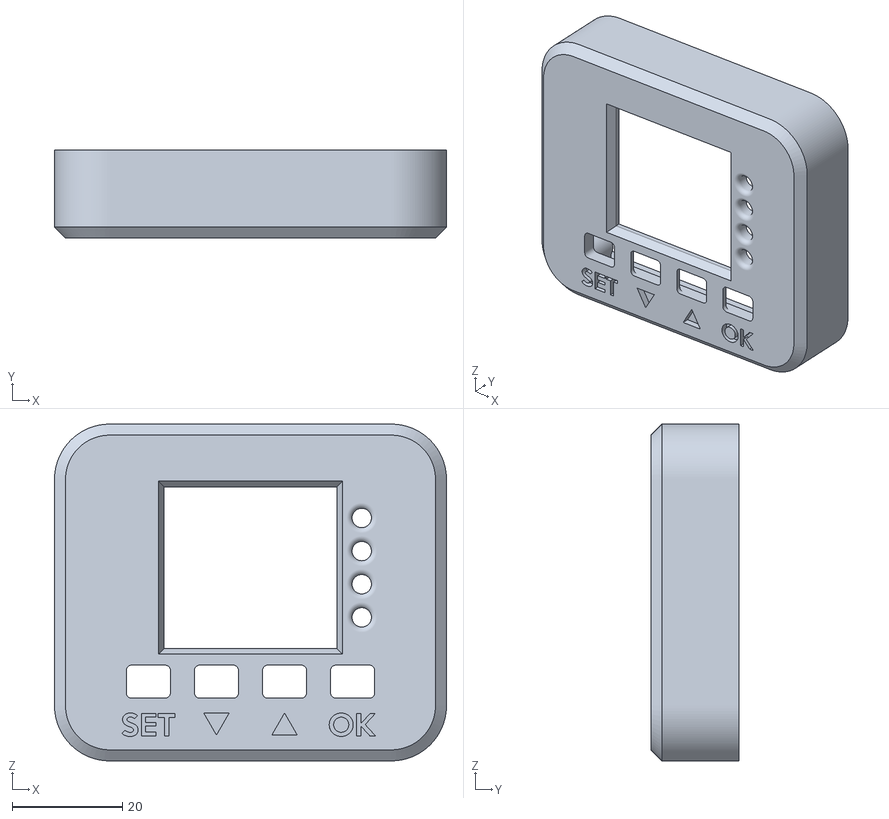
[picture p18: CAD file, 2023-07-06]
3D-files/DPM8605-Display-cover/dpm-8605-display-panel-mount-case.stl
71.0 x 16.0 x 61.0

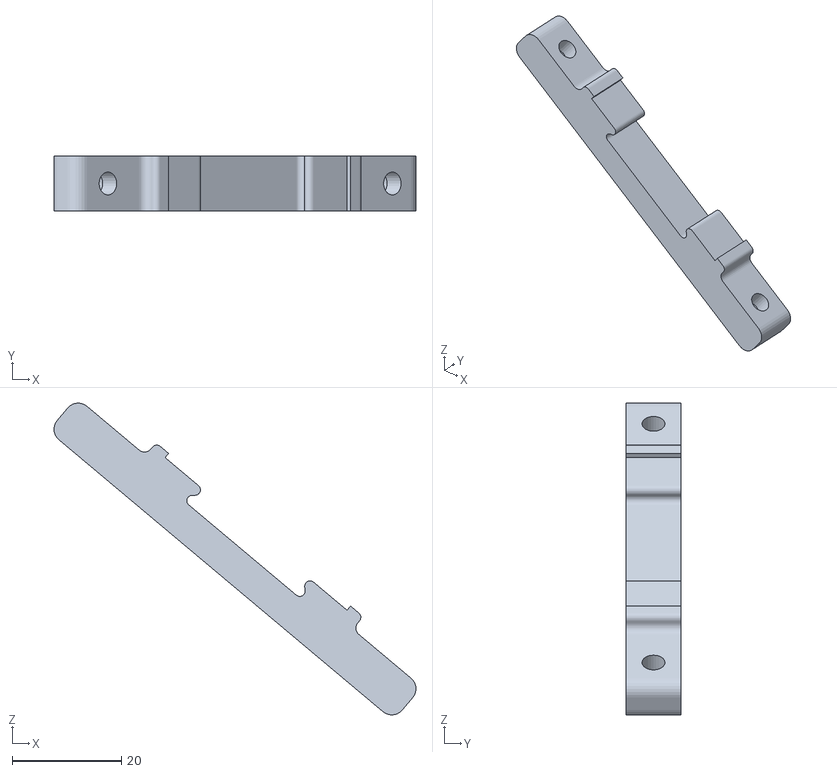
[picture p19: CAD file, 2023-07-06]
3D-files/ESP32-Controlbox/Control-panel-display-bracket-2x.stl
66.3 x 10.0 x 57.1

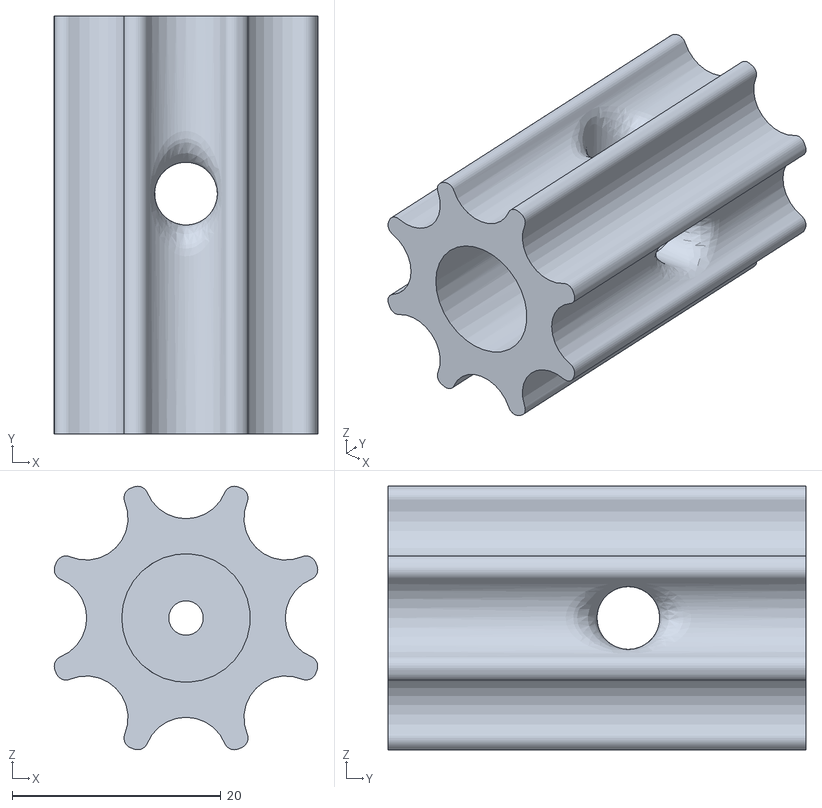
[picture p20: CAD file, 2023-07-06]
3D-files/G-EDM-Tower/printed-parts/accessories/ecm-work-in-progress-ignore-for-now/3.3mm-top-plug-tmp.stl
25.2 x 40.0 x 25.2

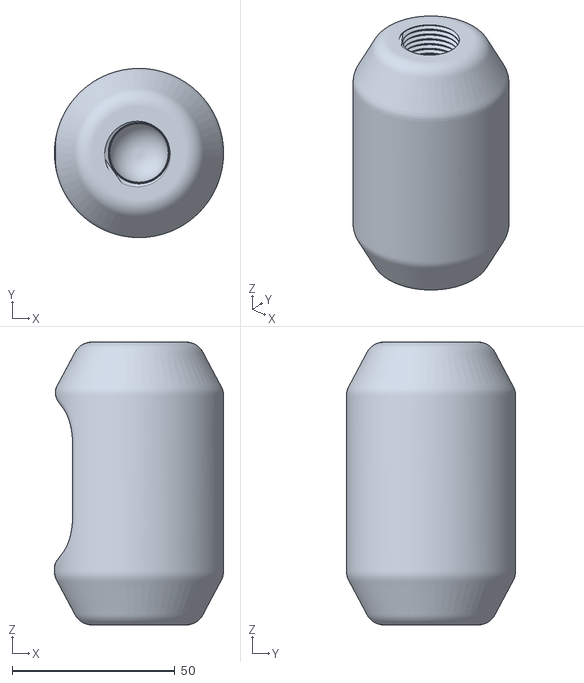
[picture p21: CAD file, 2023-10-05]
3D-files/G-EDM-Tower/printed-parts/accessories/G12-to-4mm-push-in-fittings.stl
52.0 x 52.0 x 87.0

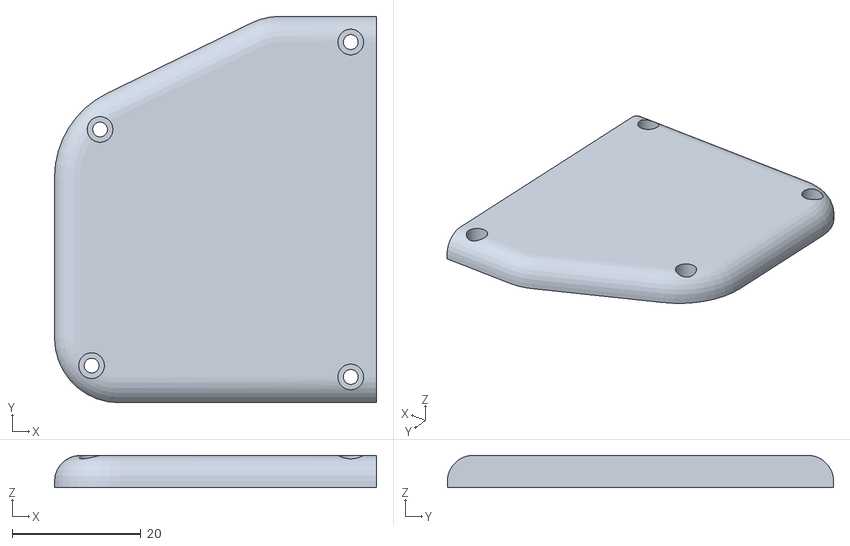
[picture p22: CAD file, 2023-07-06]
3D-files/G-EDM-Tower/printed-parts/accessories/pump-spindle-switch-box/switch-box-right-side.stl
50.0 x 60.0 x 5.00

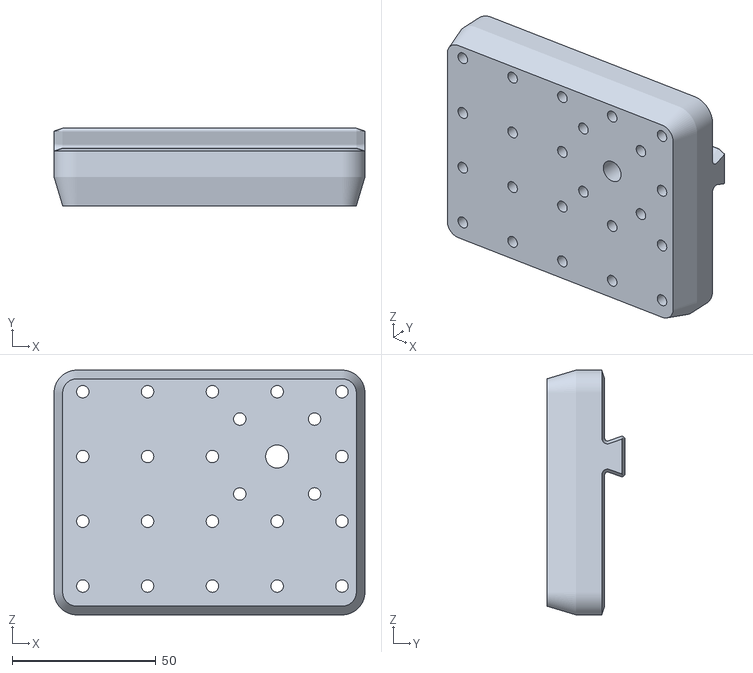
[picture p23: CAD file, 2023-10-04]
3D-files/G-EDM-Tower/printed-parts/accessories/rotary-mounting-table/wire-table-mount-adapter.stl
108.0 x 27.0 x 85.0

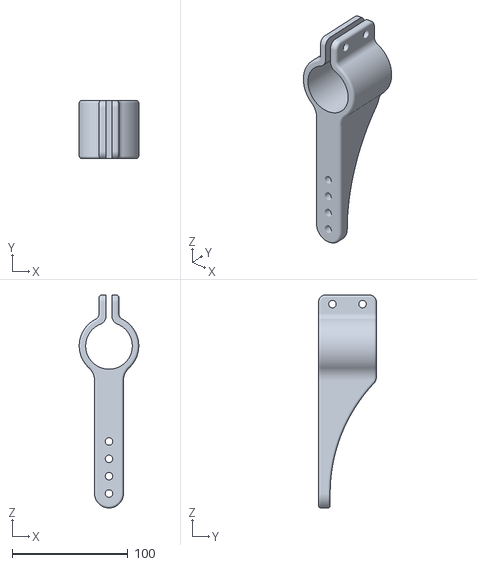
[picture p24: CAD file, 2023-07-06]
3D-files/G-EDM-Tower/printed-parts/accessories/round-bar-jig-strong-version-recommended/clamp-adapter-to-transform-the-40mm-tube-to-a-huge-clamp.stl
51.5 x 50.0 x 184.1

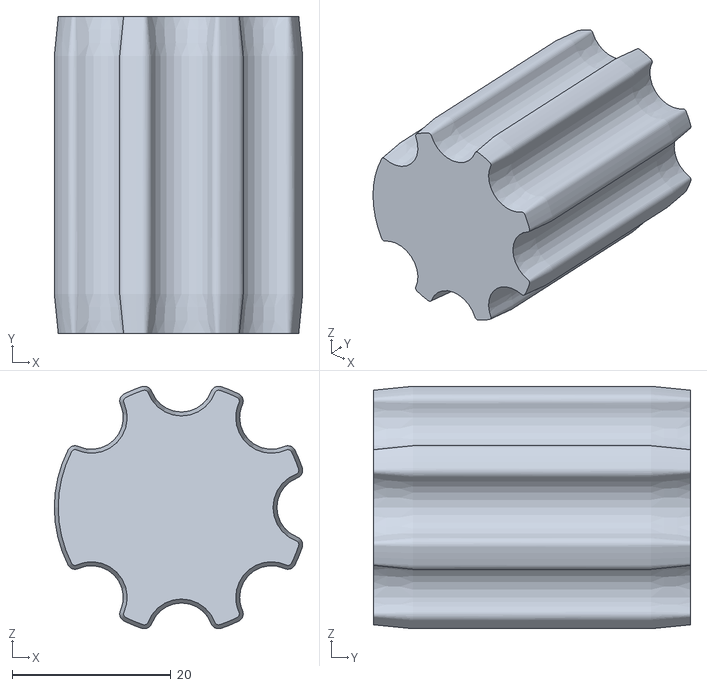
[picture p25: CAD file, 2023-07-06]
3D-files/G-EDM-Tower/printed-parts/accessories/round-bar-jig-strong-version-recommended/reamer/40x32mm-jig-reamer-bottom-plug-5.3mm-(32mmDIA).stl
31.3 x 40.0 x 30.6

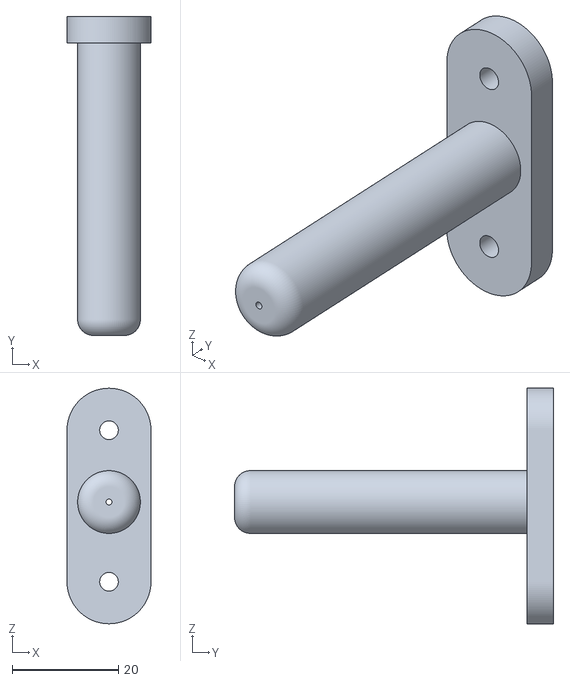
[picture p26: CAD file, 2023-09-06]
3D-files/G-EDM-Tower/printed-parts/tool-guides/tool-guide-1.1.stl
15.8 x 60.0 x 44.3

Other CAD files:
3D-files/G-EDM-Tower/printed-parts/work-in-progress/entry-level-gedm/Geared-Nema17-Motor-bracket.stl
3D-files/G-EDM-Tower/printed-parts/work-in-progress/wire-extension/spool-holder-rotary-dampener-brake-ufo.stl
3D-files/G-EDM-Tower/printed-parts/work-in-progress/wire-extension/wire-extension-v2/water-jet-nozzle-bottom.stl
3D-files/G-EDM-Tower/printed-parts/x-axis/x-axis-HGR20-block-spacer-x4.stl
3D-files/DPM8605-Display-cover/dpm-8605-display-panel-mount-buttons-TPU.stl
3D-files/ESP32-Controlbox/Control-panel-TPU-feet.stl
3D-files/ESP32-Controlbox/Control-panel-connector-panel.stl
3D-files/ESP32-Controlbox/Control-panel-left-side.stl
3D-files/ESP32-Controlbox/Control-panel-right-side.stl
3D-files/ESP32-Controlbox/Control-panel-top-lid.stl
3D-files/G-EDM-Tower/printed-parts/accessories/foot-back-big.stl
3D-files/G-EDM-Tower/printed-parts/accessories/foot-front-small.stl
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

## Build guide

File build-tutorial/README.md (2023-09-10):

# About the partlists

    The GEDM-Tower partlist may not be complete and may miss some parts. It is a work in progress. 

# Some build tips

    Whenever possible it is adviced to re-melt critical position on the parts. This machine is meant to be strong and some screws are very tight. To prevent layer separation under high torque at least the holes should be remelted.
    
    I use a normal lighter to do this and just burn the position until it starts to get glassy. For holes it doesn't matter if it starts to burn for a short time.
    
    This increases the strength heavily!
    
    If a normal lighter is used and the part is not black be careful to use the blue part of the flame. The red/orange part will produce black spots.

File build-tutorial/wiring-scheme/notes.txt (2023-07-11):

Both pulseboards are wired the same way. 

PWM IN/GND
VSense OUT (GND not connected)
30-60V Spark Power
Spark out +-
12v +-

The 12v to the pulseboard should be connected directly to the PSU terminal.

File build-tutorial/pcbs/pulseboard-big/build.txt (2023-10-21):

 
 # Transistors
 
 Q8      = PNP 2SB688 BJT power transistor 
 Q7, Q10 = NPN 2SD718 BJT power transistor
 
 # Mosfets
 
 Q1, Q2, Q3, Q4, Q5, Q6 = IRFP260N Mosfet ( mounted on the bottom side with the blank drain metal to the heatsink )
 
 # Optocoupler
 
 U1 = DIP8 Socket with 6n137 ( I recommend to not solder the optocoupler directly to the PCB and use a DIP8 socket instead )
 
 # LEDs ( optional )
 
 D16 = Low current LED green 
 D15 = LED blue
 
 # Ceramic disc capacitors
 
 C1, C10, C23 = 100nf 50V ceramic capacitors
 C9, C11, C14 = 100pF >100v ceramic capacitors
 
 # Capacitors
 
 C4  = 100uF >100V photo flash or low ESR capacitor
 C19 = 220uf 100v capacitor
 C2, c12 = 680uf 25v capacitor
 
 # Bridges ( I clipped of two legs from a 5W resistor and bend them into a U shape. See the images for details )
 
 R30, R31 

 # Diodes
 
 D1, D3, D6, D7, D10, D12   = SB 140 DIO Schottkydiode, 40 V, 1 A, DO-15 ( fast turn off diodes for Mosfets )

 # Resistors
 
R8, R9, R14, R15, R19, R22 = 100kOhm 1W ( pulldown resistor for the mosfet gate )
R6, R7, R12, R13, R18, R21 = R4.7 2W    ( Mosfet gate resistors. Value could change to 6.8Ohm later if it works better. )

R3 = R560 5W axial
R4 = R560 2W

R1  = R220 1W
R29 = R200 1W
R2  = 4.7kOhm 2W
R33 = 4.7kOhm 2W
R28 = R560 1W
R5  = 1kOhm 1W

# Trim Pot

RV1 = 10kOhm 3296 Trim Pot

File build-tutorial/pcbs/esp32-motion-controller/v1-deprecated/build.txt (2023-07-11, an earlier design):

# Notes

    Parts that are not listed here are not connected
    For example D1, J9, C1, R1, C4, C9 are not used

# capacitors

    C2, C3, C6 = 100nF 50v ceramic disc capacitor
    C8         = 680uf 25v capacitor
    C5         = 47uf 63v capacitor ( this can be a 680uf 16v capacitor too, I just used what I had around at that time. )
    C7         = 680uf 16v capacitor

# Resistors

    R3, R5 = 1kOhm   1/2W resistor
    R2, R4 = 100kOhm 1/2W resistor

# Dip switches

    SW1 = 4 pole dip switch

# Pin headers

    J1, J2, J4, J9, J10, J11, J12, J13 = Pin headers ( can be cut to size )

# Pin sockets

    J5, J6, U1, U2, U3, U4 = Pin sockets ( don't solder the ESP or TMC directly on the PCB! )

# Screw Terminals

    J7, J8, J15, J17 = 4 pole screw terminal
    J18              = 2 pole screw terminal

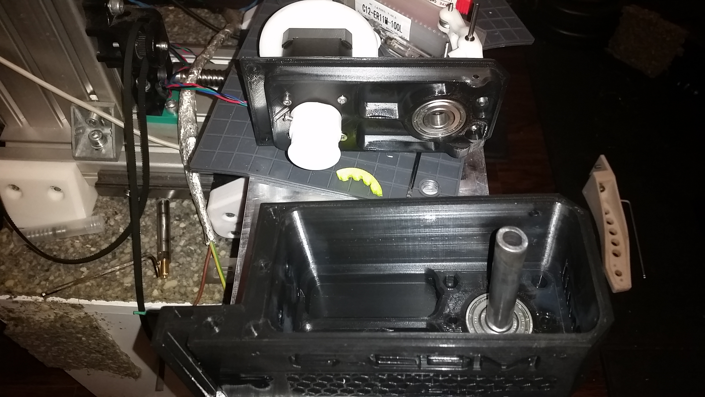
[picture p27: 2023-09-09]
images/build/tool-head/3.jpg

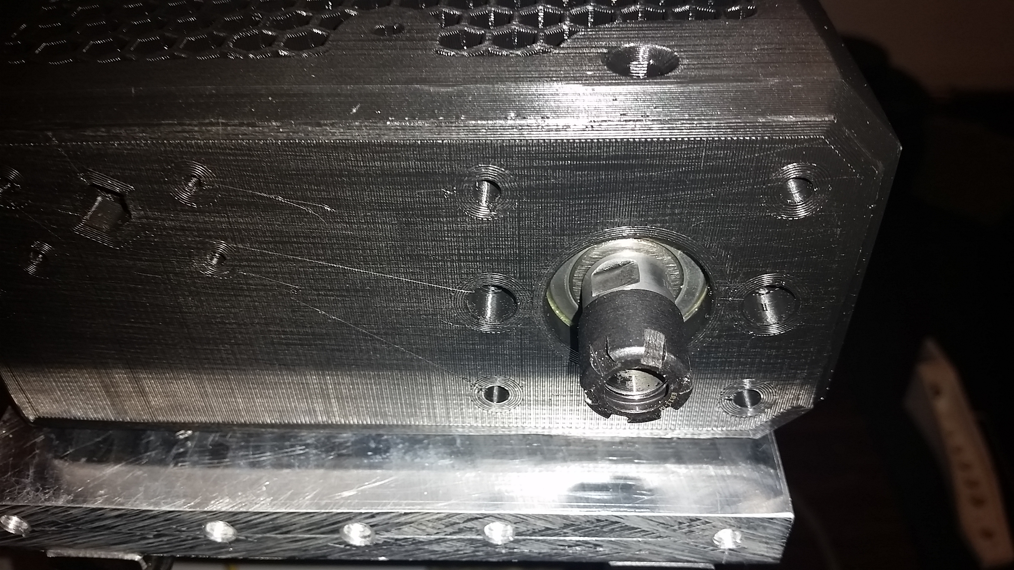
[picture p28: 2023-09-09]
images/build/tool-head/1.jpg

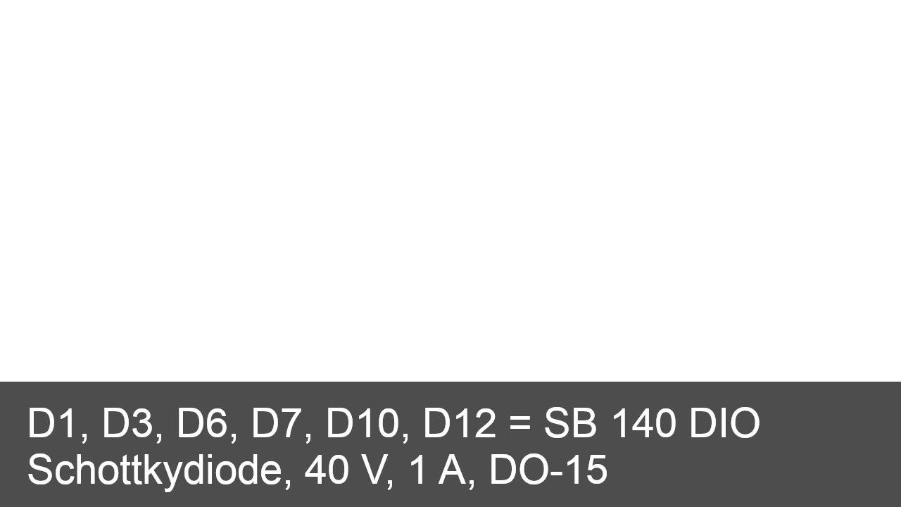
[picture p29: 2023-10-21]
build-tutorial/pcbs/pulseboard-big/big-pulseboard-tutorial/text-images/15.png

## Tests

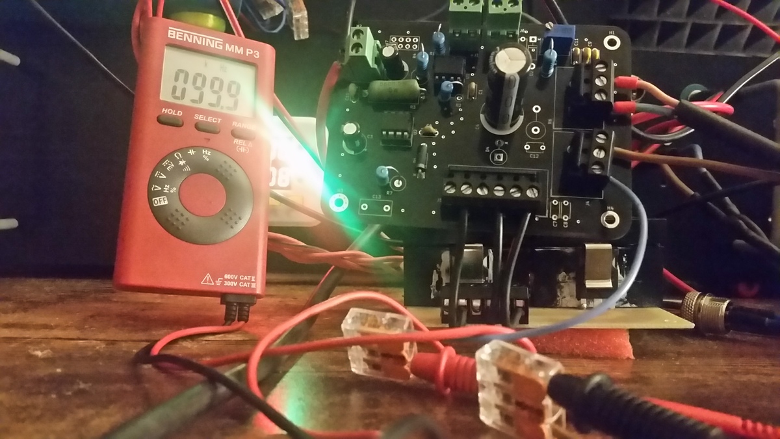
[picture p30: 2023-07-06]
images/pcbs/pulseboard-small/test2.jpg

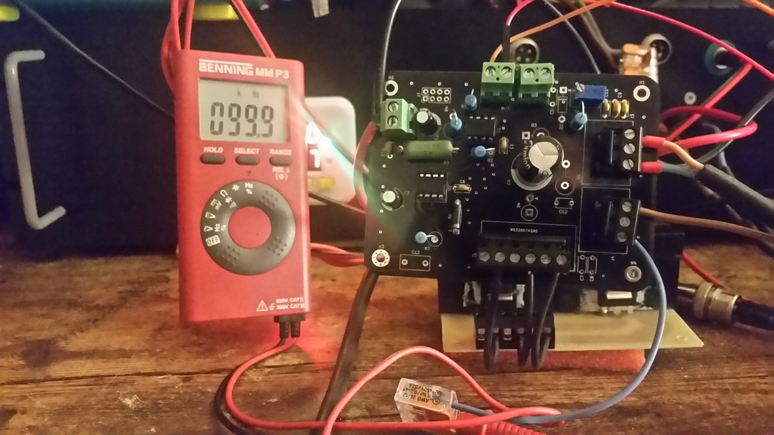
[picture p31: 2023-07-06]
images/pcbs/pulseboard-small/test.jpg

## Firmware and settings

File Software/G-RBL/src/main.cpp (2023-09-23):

// Remove all serial.prints


/*
#  ██████        ███████ ██████  ███    ███  
# ██             ██      ██   ██ ████  ████  
# ██   ███ █████ █████   ██   ██ ██ ████ ██ 
# ██    ██       ██      ██   ██ ██  ██  ██ 
#  ██████        ███████ ██████  ██      ██ 
#
# This is a beta version for testing purposes.
# Only for personal use. Commercial use or redistribution without permission is prohibited. 
# Copyright (c) Roland Lautensack        
*/   

//################################################
// Main includes
//################################################
#include <driver/adc.h>
#include "gedm_main.h"
#include "config/definitions.h"
#include "sd_card/filehandler.h"

//################################################
// GRBL_ESP32
//################################################
#include "Grbl.h"

//#include <Arduino.h>

String active_profile = "None";

/** task related **/
TaskHandle_t vsense_task     = NULL;
TaskHandle_t start_stop_task = NULL;
TaskHandle_t ui_task_handle  = NULL;

void start_services(){
  // main tasks for the UI and touch
  ui_controller.start_ui_task();
  // sensor service includes the vSense feedback and the EDM start stop switch
  ui_controller.run_sensor_service();
}

void update_ui_controller(){
    ui_controller.set_voltage_min( source_voltage_min );
    ui_controller.set_drop_min_max( vsense_drop_range_min, vsense_drop_range_max );
    ui_controller.set_drop_short(VSENSE_DROP_RANGE_SHORT);
    ui_controller.set_drop_min_max( vsense_drop_range_min, vsense_drop_range_max );
    ui_controller.set_voltage_min( source_voltage_min );
    ui_controller.set_ms_edm( STEPPER_MOTOR_MICROSTEPS_EDM );
    ui_controller.set_ms_travel( STEPPER_MOTOR_MICROSTEPS_TRAVEL );
    ui_controller.set_min_max( PWM_FREQUENCY_MIN, PWM_FREQUENCY_MAX );
    ui_controller.change_pwm_frequency( ( int ) pwm_frequency );
    ui_controller.update_duty( pwm_duty );
    ui_controller.set_pwm_pin( GEDM_PWM_PIN );
    ui_controller.setup_pwm_channel();
    ui_controller.disable_spark_generator();
}


void setup() {
    if( ENABLE_SERIAL ){
      Serial.begin(9600);
    }
    disableCore0WDT();
    disableCore1WDT();
    grbl_init();
    ui_controller.init();
    ui_controller.set_filehandler( &filehandler );
    update_ui_controller();
    start_services();
    ui_controller.set_is_ready();
}

void loop(){
  run_once();
  vTaskDelay(2000);
}

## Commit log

2023-08-22 partlist added
    [tool-guide-1.2.stl, tool-guide-1.stl, tool-guide-prototype.FCStd]
2023-08-30 added ESP32 pinout
2023-09-06 new parts added
    [rewinder-spool-bottom.stl, rewinder-wire-guide-lever.stl, rewinder-wire-guide-main.stl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]
2023-09-09 partlist update ER11M C12 shaft
    [logo-tutorial.FCStd, wire-extension-main-brake-system.stl, wire-extension-main-lever.stl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]
2023-09-10 toolhead belt updated
    [GT2-Belt-224mm-112T-10mm.stl, GT2-closed-TPU-belt-116T-232mm.stl]
2023-09-14 build-tutorial wiring the wire extension
2023-09-18 build-tutorial updated
    [rewinder-spool-top.stl, spool-holder-bottom.stl, spool-holder-rotary-dampener-brake-ufo-TPU-insert.stl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]
2023-09-22 small update
    [deprecated-not-needed-wire-extension-main-brake-system.stl]
2023-09-28 small updates
    [adjustable-wire-guide-main.stl, deprecated-not-needed-wire-extension-main-brake-system.stl, water-jet-nozzle-top.stl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]
2023-09-30 bugfix for PWM issue with MCPWM
2023-10-02 added a wire gcode example
    [rickandmorty_logo.FCStd]
2023-10-04 added more images
    [wire-table-mount-adapter.stl]
2023-10-05 fixed some typos
    [G12-to-4mm-push-in-fittings.stl, water-jet-nozzle-bottom.stl]
2023-10-05 removed grbl
2023-10-19 partlist update
    [z-axis-GT2-6mm-pulley-for-geared-nema17-T30.stl, z-axis-GT2-6mm-pulley-for-geared-nema17.stl]
2023-10-28 added wire extension cad file
